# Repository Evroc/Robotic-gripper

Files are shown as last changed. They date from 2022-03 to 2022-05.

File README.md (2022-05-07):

# Robotic gripper

## Table of contents
  1. [Introduction](#introduction)
  1. [Features](#features)
  1. [Printed parts](#printed-parts) 
  1. [Other parts](#other-parts)
  1. [PCB](#pcb)
  1. [Software](#software)
  1. [Simulation](#simulation)
  1. [Assembly manual](#assembly-manual)
  1. [Additional informations](#additional-informations)
  1. [Other links](#other-links)

## Introduction

 Cheap, 3d printed gripper for robotic applications with integrated electronics and ROS communication.
    
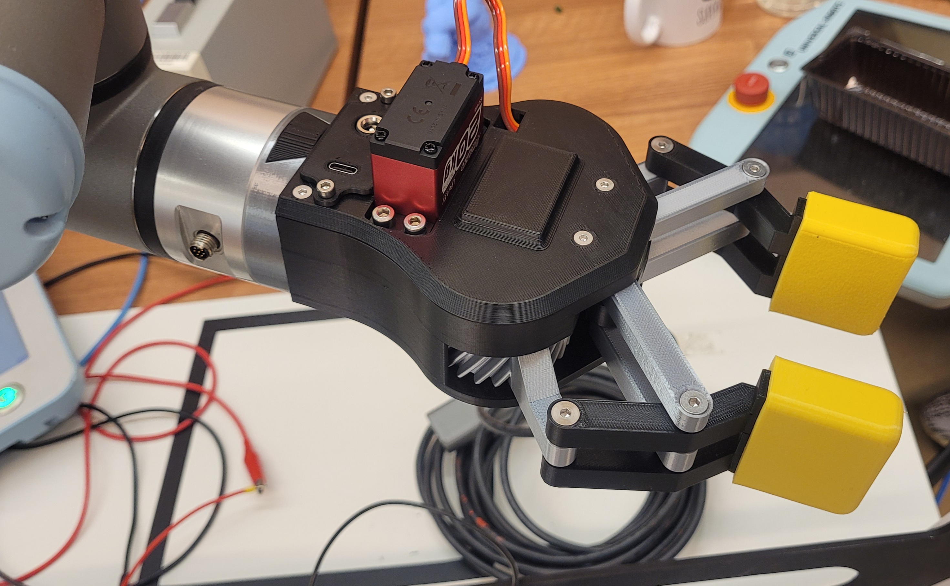
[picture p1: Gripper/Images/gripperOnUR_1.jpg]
Gripper mounted on UR3e


## Features

* The gripper is mostly 3D printed, all parts were designed for FDM printers.

* Cheap - <100$ (excluding 3d printed parts), the most expensive parts are servomechanism and microcontroller.

* Powerful grip - 2:1 gear ratio.

* Plug’n play - after assembling the project all you need to do is connect a USB-C cable and power cord
to DC socket.

* Easy communication - you can simply send the servo position using a USB-C cable and provided code
example.

* ROS compatible - use rosserial to communicate with the gripper.

## Printed parts

All files can be found there: ([LINK](https://www.printables.com/model/165722-robotic-gripper))

## Other parts
  
For non printed parts look here:

* Gripper parts [CLICK](/Gripper/BOM/GripperBOM.xlsx)

* PCB parts [CLICK](/PCB/BOM/PCB_BOM.xlsx)

## PCB

I designed dedicated PCB for this project, however feel free to modify it or even use your own designs.
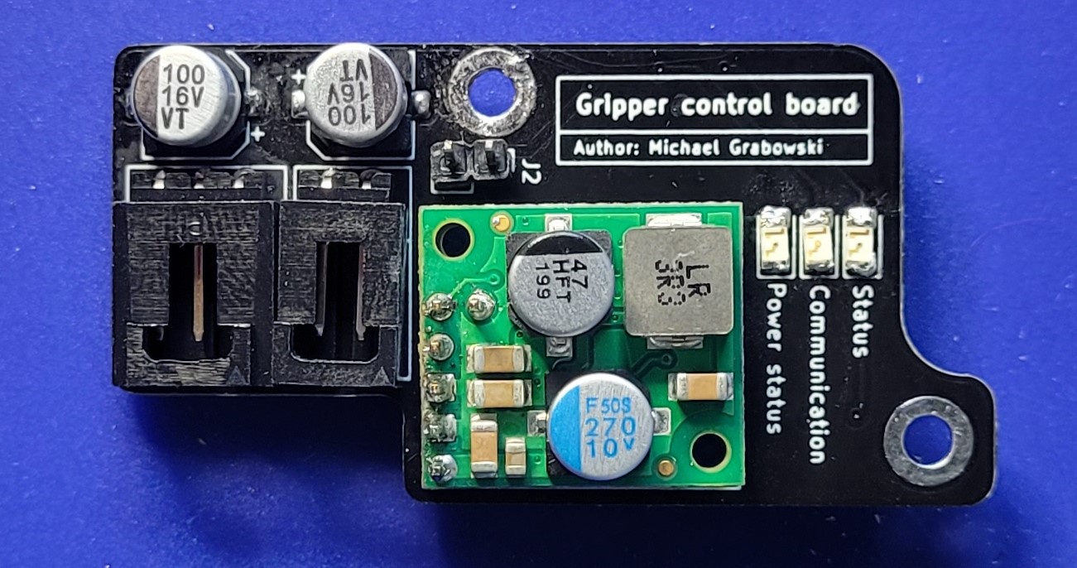
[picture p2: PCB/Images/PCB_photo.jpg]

  
 Cheatsheet:
 * STATUS led - pin 0 (pinMode(0, OUTPUT))
 * COMMUNICATION led - pin 1 (pinMode(1, OUTPUT))
 * SERVO - pin 8 (servo.attach(8))
 * Power Status led works independently from the software
 * Jumper allows to power MCU without USB cable
  
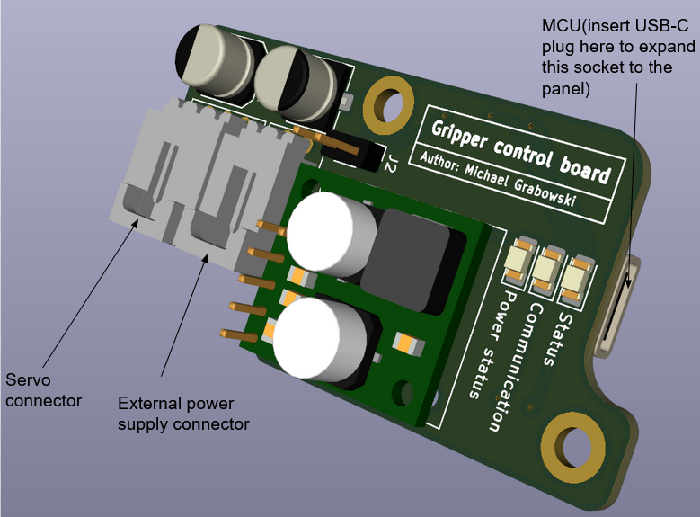
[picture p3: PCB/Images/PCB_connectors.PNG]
 

## Software

The repository includes two exemplary control methods:
- using the serial library
- using the rosserial package and the ROS platform

The included examples are written in Python language.

In order to upload the program to Seeeduino, the appropriate Arduino IDE configuration is necessary ([instruction](http://wiki.ros.org/ROS/Installation))

For both options it is necessary to install the pyserial library:
```
$ pip3 install pyserial
```
To use example with pyserial:
* upload to Seeeduino program gripper_serial.ino
* run the script gripper_serial.py with the appropriate port as an argument:
```
$ python3 gripper_serial.py --usb_port /dev/ttyACM0
```

To use example with rosserial: 
* upload to Seeeduino program gripper_rosserial.ino
* install ROS ([installation instruction](http://wiki.ros.org/ROS/Installation))
* create a workspace and build rosserial repository:
```
$ mkdir -p catkin_ws/src
$ cd /catkin_ws/src
$ git clone https://github.com/ros-drivers/rosserial.git
$ cd /catkin_ws
$ catkin_make
$ source devel/setup.bash
```
* run roscore in another terminal
* run serial_node with the appropriate port as an argument:
```
$ rosrun rosserial_python serial_node.py port:=dev/ttyACM0
```
* in another terminal run script gripper_rosserial.py
* you can also control gripper by publish state on the topic /gripper_state, for example:
```
$ rostopic pub /gripper_state std_msgs/Int16 "data: 0"
```
## Simulation

Check that: https://github.com/Michal-Bidzinski/UR3_sim

## Assembly manual
  
Online version is here: ([Build guide](https://1drv.ms/p/s!AmhhxRqSkzTrhK5689f8yG8gnyS89Q?e=EBmXII)) 
  
PDF is here: [Build guide PDF](/Build_guide/GripperBuildGuide_v1.0.pdf)

## Additional informations
  
Keep in mind that the project is still under development and some information is missing here. If you encounter problems - contact me using email: michael.grabowski.lab@gmail.com
  
## Other links

  ([Assembly animation](https://www.youtube.com/watch?v=25BgIXnhyFg))
  
  ([How does the mechanism works](https://youtu.be/p2rVJ_NBgKo))

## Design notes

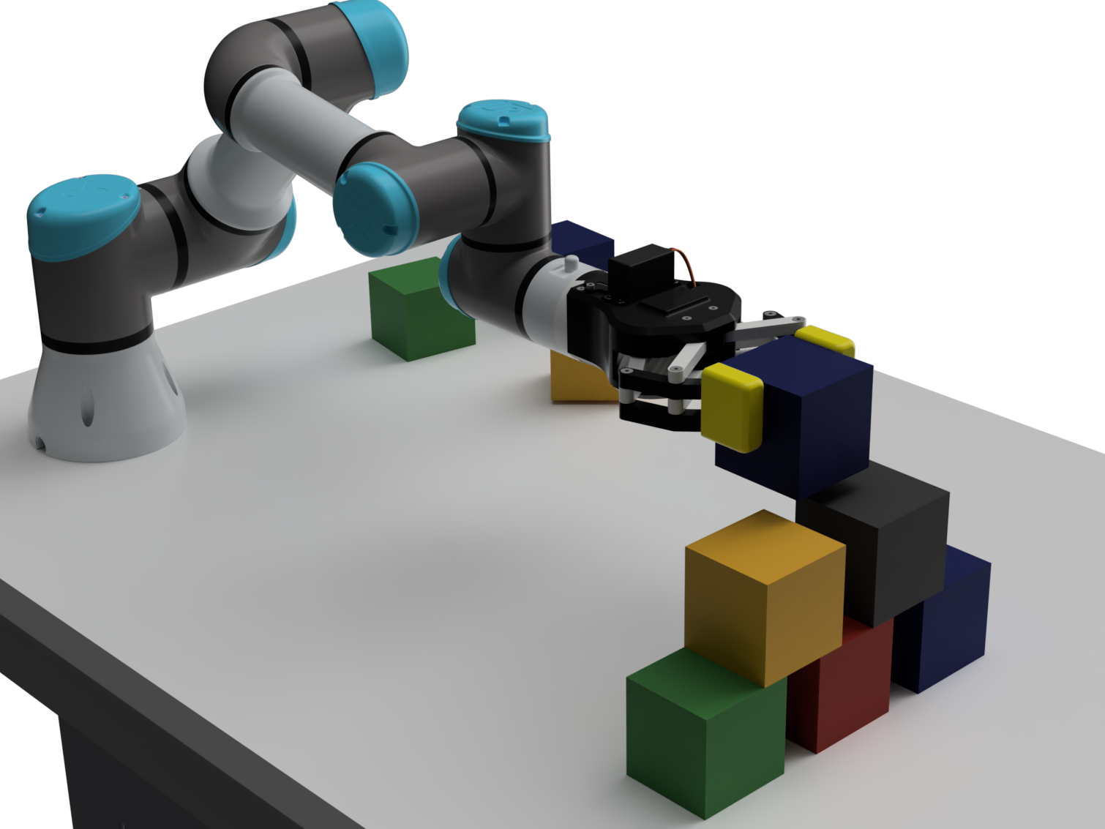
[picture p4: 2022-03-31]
Gripper/Images/RenderWithUR1.png

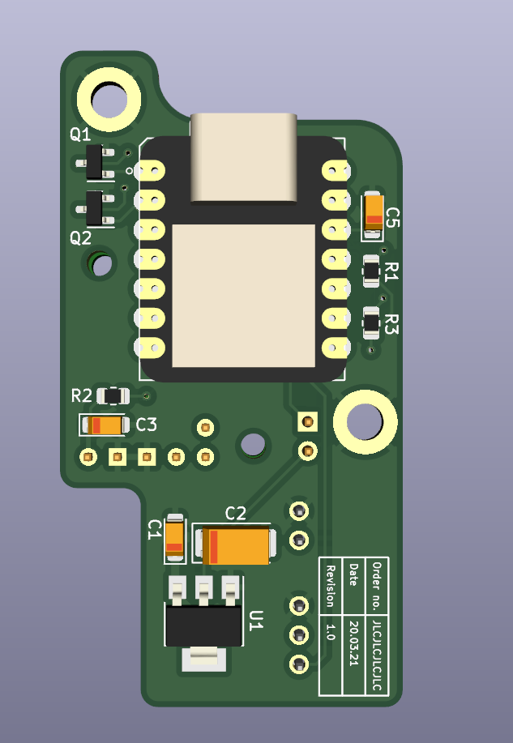
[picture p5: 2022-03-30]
PCB/Images/BottomView.png

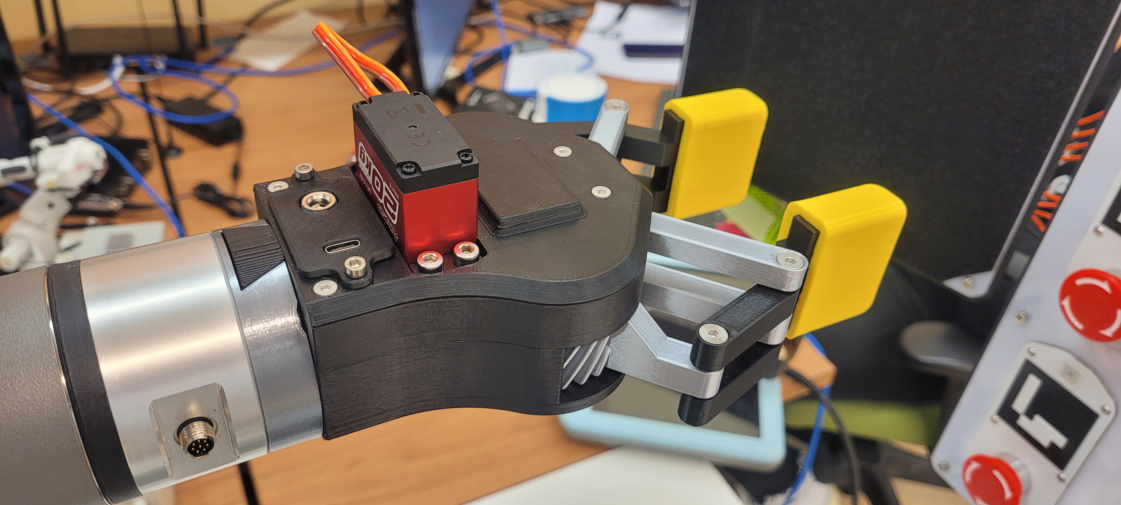
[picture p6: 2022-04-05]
Gripper/Images/gripperOnUR_3.jpg

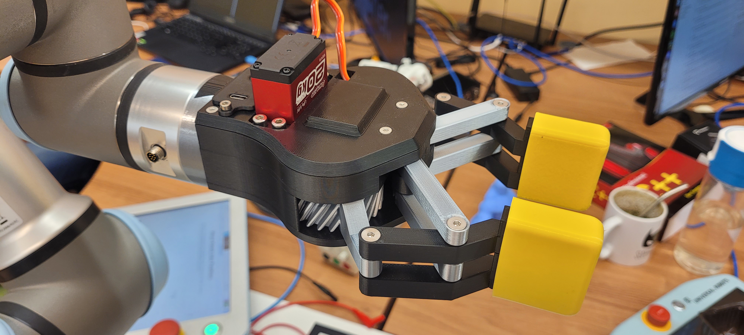
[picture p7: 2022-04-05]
Gripper/Images/gripperOnUR_2.jpg

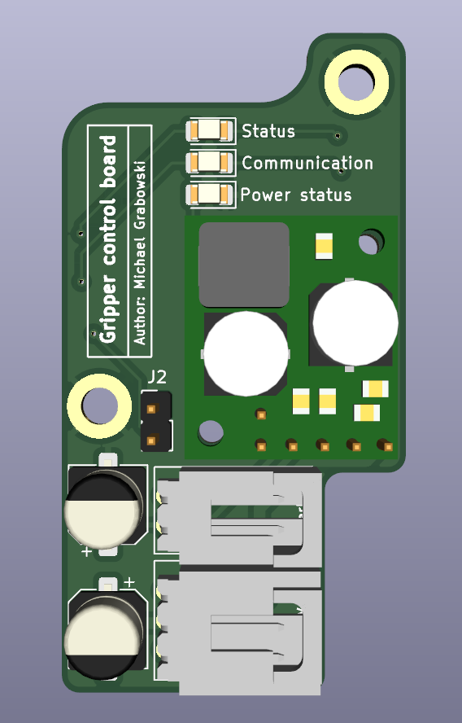
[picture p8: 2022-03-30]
PCB/Images/TopView.png

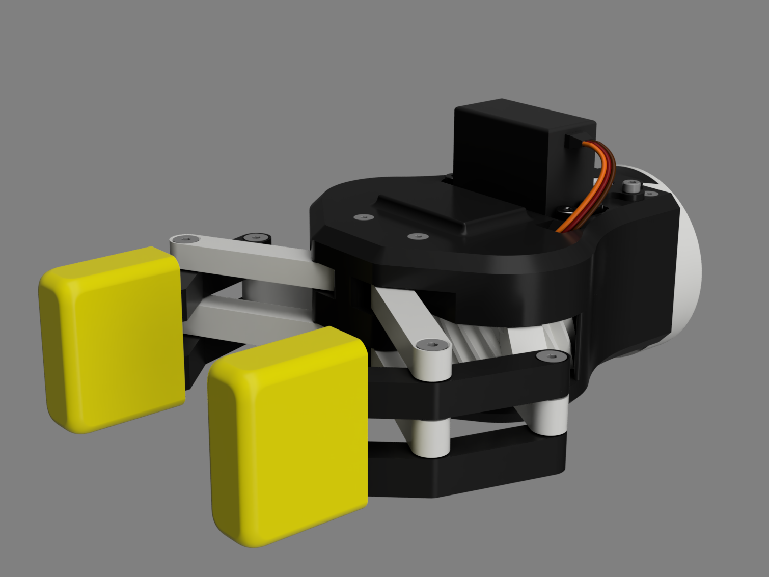
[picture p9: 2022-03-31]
Gripper/Images/RenderGripper.png

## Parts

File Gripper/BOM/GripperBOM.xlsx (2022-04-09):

Screws and nuts
 |  |  |  |  |  |  |  | You may use the gripper with an external control system(f.e. arduino with a breadboard etc.)-then you don’t need sockets, plugs, connectors, etc.
Size | Item | Type | Length | Amount | Application
M3 | Screw | Socket cap | 4mm | 6 | PCB to base, panel mount, usb-c mount
M3 | Screw | Flathead | 10mm | 4 | Top to mid(base) |  |  |  | must have
M3 | Screw | Flathead | 16mm | 2 | Spacer to bottom(base) |  |  |  | optional
M3 | Screw | Flathead | 8mm | 1 | ServoGear to servo
M3 | Screw | Headless | 10mm | 4 | ServoHorn to servogear
M4 | Screw | Socket cap | 8mm | 4 | Servo to mid(base)
M4 | Screw | Flathead | 30mm | 3* | Arms to gears +base to adapter
M4 | Screw | Flathead | 35mm | 2 | Mid to bottom (base)
M4 | Screw | Flathead | 40mm | 2 | Sticks to arms
M4 | Screw | Flathead | 45mm | 3 | Mid to bottom(base), axles for sticks
M4 | Nut | Nylock |  | 4 | Bottom arms
M4 | Nut | Square |  | 3* | Base connections+adapter
 |  |  | *1 less if you don’t need the robot-gripper adapter
Other mechanical parts
 |  |  |  |  |  | Sample links
Item |  | Size | Amount
Cylindrical rollers |  | 5x8mm | 5 |  |  | https://www.ebmia.pl/waleczki/37040-walek-waleczki-5x8-skf.html
Ball bearing |  | 5x13x4mm | 5
Round aluminium servo horn |  |  | 1
Electronic parts(not included in PCB BOM)
Item |  | Size | Amount
Servo |  | Standard | 1 |  |  | https://botland.store/standard-servos/3576-servo-powerhd-lf-20mg-standard-6939670200387.html
SparkFun USB-C Breakout |  | Standard | 1 |  |  | https://www.sparkfun.com/products/15100
DC socket |  | 2,1/5,5mm | 1
HZ03 Connector with pins |  |  | 1 |  | Connecting servo to the control board | https://en.maritex.com.pl/connectors/crimp_terminal_connectors/crimp_terminal_2_54mm_pitch/female_crimp_terminal_housings_for_cable_with_snap-lock_2_54_mm_pit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
HZ02 Connector with pins |  |  | 1 |  | Connecting DC socket to the control board | https://en.maritex.com.pl/connectors/crimp_terminal_connectors/crimp_terminal_2_54mm_pitch/female_crimp_terminal_housings_for_cable_with_snap-lock_2_54_mm_pit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
USB-C male plug(to solder wires) |  |  | 1 |  | Connecting USB-C socket to the microcontroller | https://www.amazon.com/Solder-Cable-Socket-Attached-Board/dp/B07P1BDNQV
Wires |  |  |  |  | Connectors
 |  |  |  |  |  |  | You may use angled goldpins connectors instead of WZ03/02 - then you don’t need HZ03/02 connectors

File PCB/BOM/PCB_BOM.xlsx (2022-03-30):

Electronic components
Reference on schematic | Type | Value | Case | Comment
C1,C3,C5 | Tantalum Capacitor | 10uF | Kemet-C
C2 | Tantalum Capacitor | 100uF | Kemet-A
C4, C6 | Electrolitic Capacitor | 100uF | SMD 6.3x5.8
D1 | LED |  | SMD1206 | Yellow
D2 | LED |  | SMD1206 | Red
D3 | LED |  | SMD1206 | Blue
PowerInput1 | Connector | WZ02R
Q1,Q1 | NPN BRT |  | SOT-23
R1 | Resistor | 100 | SMD0805
R2 | Resistor | 330 | SMD0805
R3 | Resistor | 22 | SMD0805
U1 | LM1117-3.3 |  | SOT223
U2 | Seeduino XIAO - SAMD21 ARM Cortex M0+
U3 | D36V28F6
Servo | Connector | WZO3R
Screws and nuts
Size | Item | Type | Length | Amount
M2 | Screw | Socket cap | 8mm | 2
M2 | Nut | Hexagon |  | 2

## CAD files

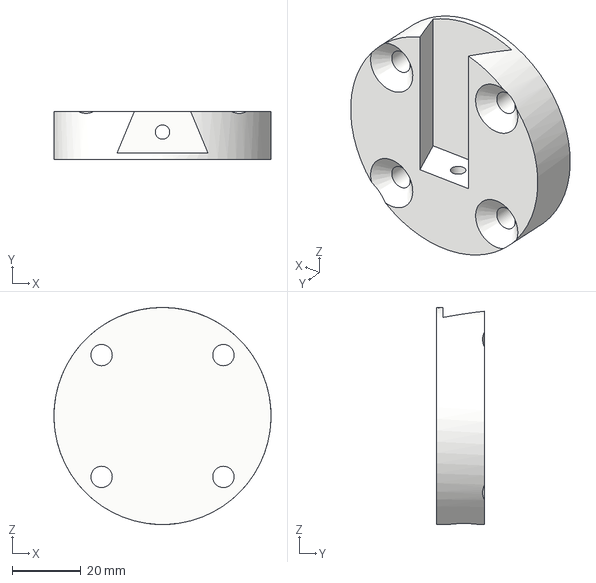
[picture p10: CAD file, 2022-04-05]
Gripper adapters/UR3/UR3_adapter.step
63.0 x 14.0 x 63.0 mm

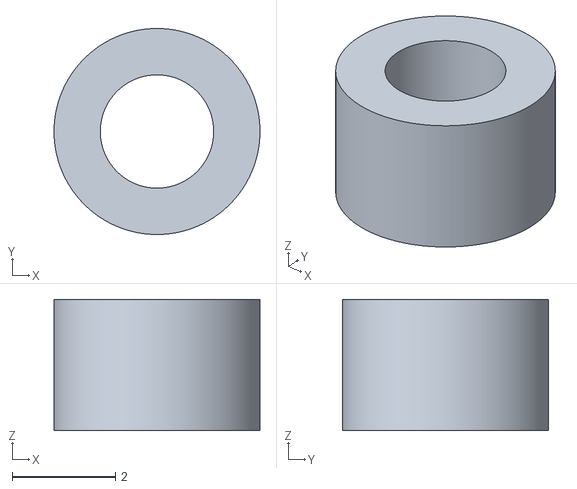
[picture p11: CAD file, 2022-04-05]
PCB/STLs/PCB_spacer.stl
4.00 x 4.00 x 2.55

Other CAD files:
Gripper adapters/UR3/UR3_adapter.stl

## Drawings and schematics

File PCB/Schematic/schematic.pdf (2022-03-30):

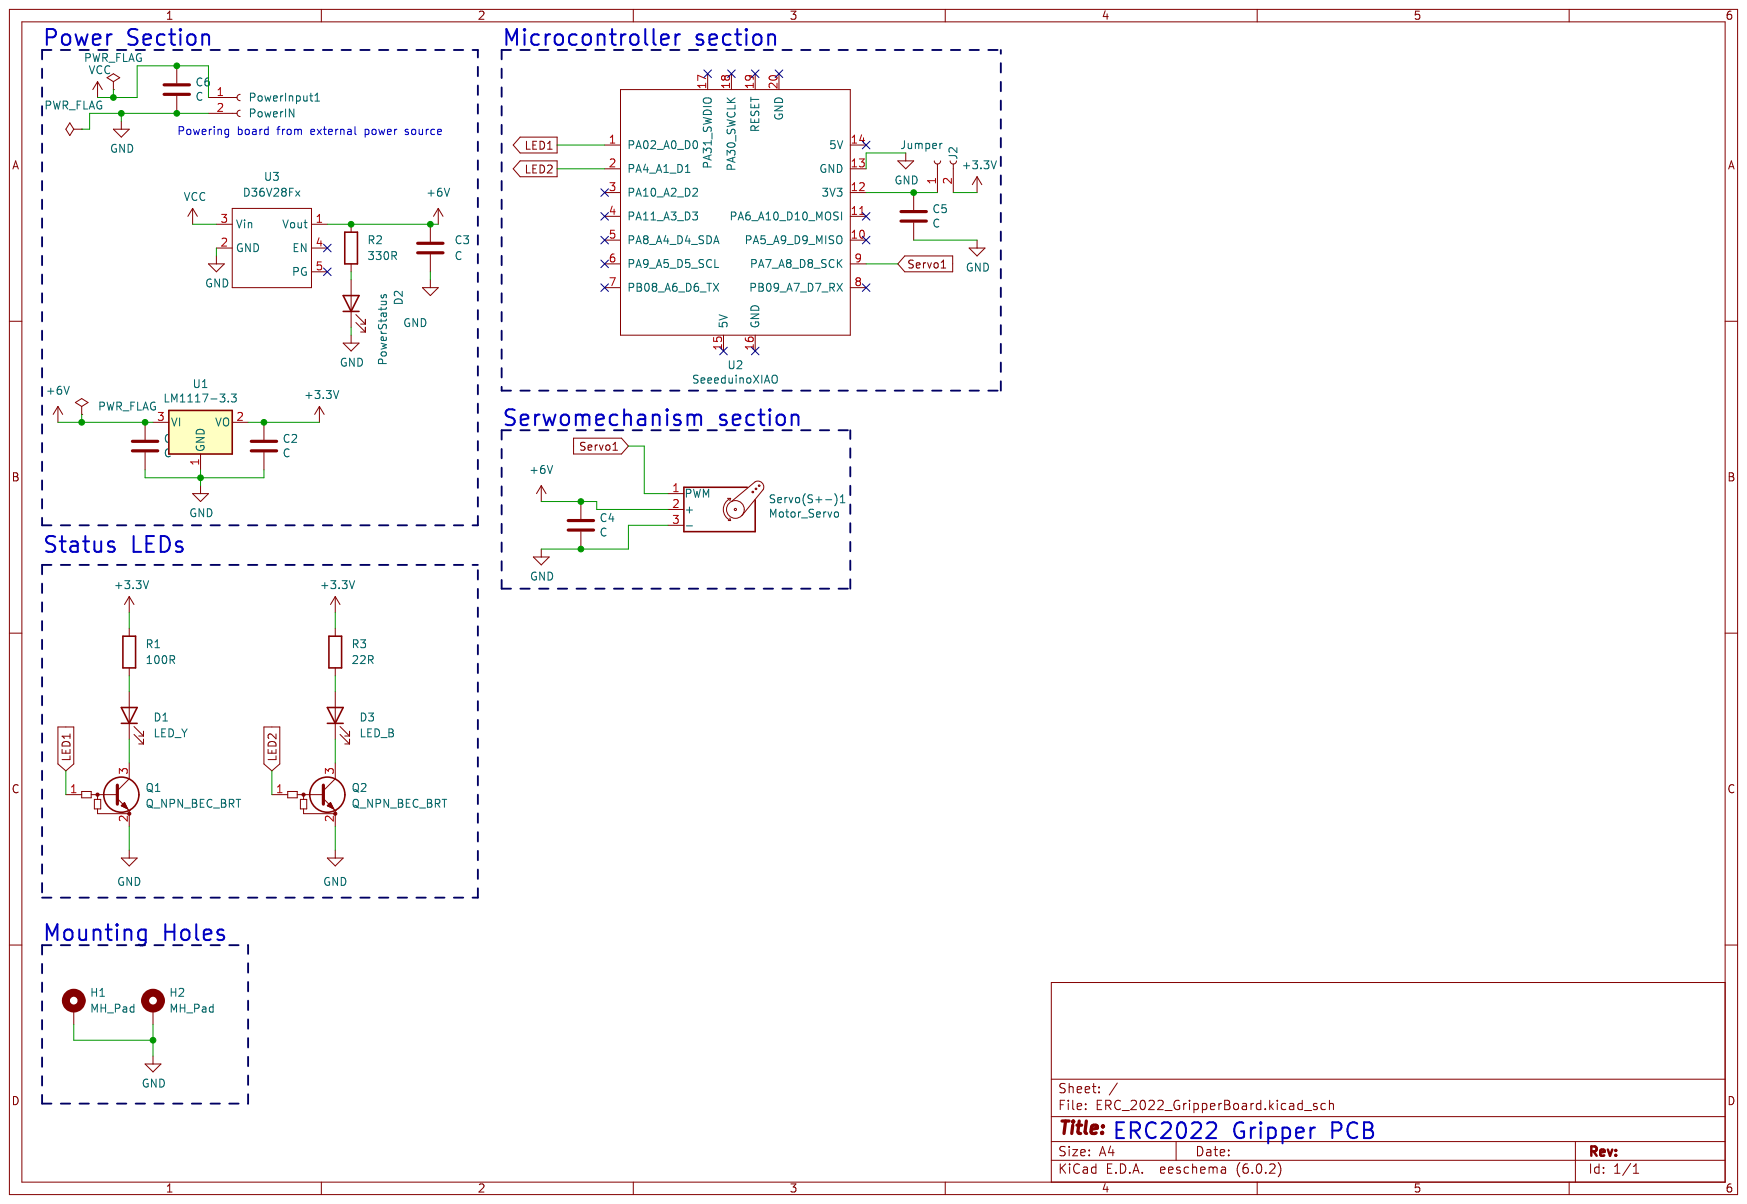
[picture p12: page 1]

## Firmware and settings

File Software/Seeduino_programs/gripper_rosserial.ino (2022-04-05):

#define USE_USBCON

#include <Wire.h>
#include <ros.h>
#include <std_msgs/Int16.h>
#include <Servo.h>

Servo servo;
ros::NodeHandle nh;


void gripperCb(const std_msgs::Int16& state)
{
  servo.write(state.data);  
}

ros::Subscriber<std_msgs::Int16> gripper_setSub("gripper_state", &gripperCb);


void setup() 
{
  nh.initNode();
  nh.subscribe(gripper_setSub);
  Serial.begin(57600);
  
  servo.attach(8);  
  servo.write(180);
}

void loop() 
{
  nh.spinOnce();
}

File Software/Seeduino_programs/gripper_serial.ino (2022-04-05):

#include <Servo.h>
Servo servo; 
String in_byte;
int state;

void setup() {
 
  servo.attach(8);
  Serial.begin(9600);
  servo.write(180);
}

void loop()
{    
  if(Serial.available()) 
  { 
    in_byte = Serial.readStringUntil('\n');
    state = in_byte.toInt();        
    servo.write(state);   
  }
}

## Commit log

2022-03-30 First commit - PCB files
    Added files related to pcb design - kicad files, gerber and drill files, some pics and bom.
    [GripperBoard-B_Cu.gbl, GripperBoard-B_Mask.gbs, GripperBoard-B_Paste.gbp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]
2022-03-31 Gripper documentation
    Added pics, short datasheet and BOM
    [GripperBOM.xlsx]
2022-04-05 Added photos and readme
    [GripperBOM.xlsx, UR3_adapter.step, UR3_adapter.stl]
2022-04-05 Updating BOM +adding pcb spacers
    [GripperBOM.xlsx, PCB_spacer.stl]
2022-04-08 Fixed BOM, added new pic
    [GripperBOM.xlsx]
